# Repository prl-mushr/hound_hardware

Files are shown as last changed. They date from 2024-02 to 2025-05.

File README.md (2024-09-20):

# Repository that contains hardware files associated to the HOUND project.
##### Note: If you already have a [MuSHR](https://mushr.io/), you will be re-using a fair number of the components, so do not order the highlighted components from the BOM, as they represent the "overlapping components". Additionally, you may want to order the d455 if you don't have one and want to use that.

## [Bill of materials](https://docs.google.com/spreadsheets/d/12jod9aALWGB2n3a47guYzTRTLul8M2QtT9iCGtkBhws/edit?usp=sharing)

## Build steps:
The build steps are divided into 2 parts:
1. Setting up the computers -- flashing Jetpack and the ardupilot board
2. Setting up the HOUND hardware

### Setting up the Jetson Orin NX:

1. For this, you will require one Desktop, and the Orin NX, along with its corresponding parts (WiFi card, SSD, heat sink). After that, follow [this video](https://www.youtube.com/watch?v=Ucg5Zqm9ZMk) to flash the operating system onto the module, but flash jetpack 5.1.2.
2. Due to bugs in the SDK manager, the SDK manager will likely flash the operating system, but fail to properly install the jetpack. If this happens, you just need to do the following:
   ```bash
    sudo apt update
    sudo apt-get install nvidia-jetpack
    sudo usermod -aG docker $USER
    sudo pip install jetson-stats
    sudo reboot now
    ```
3. For Ubuntu, download QGroundcontrol(QGC), for Windows (preferred), download MissionPlanner(MP).
4. Follow these instructions for [QGC](https://docs.qgroundcontrol.com/Stable_V4.3/en/qgc-user-guide/setup_view/firmware.html) and these for [MP](https://ardupilot.org/planner/docs/common-loading-firmware-onto-pixhawk.html) to flash the [custom firmware](https://github.com/prl-mushr/hound_hardware/tree/main/ardupilot_files/firmwares/mroPixracerPro) on to the MRo PixRacer Pro.
5. Follow this guide to load the [board parameters](https://github.com/prl-mushr/hound_hardware/blob/main/ardupilot_files/parameters/HOUND_mro_defaults.param) using QGC or MP onto the MRo Pixracer pro. (**TODO: insert images describing this step**)

### Setting up the Hardware:
#### Setting up the base (These steps are a WIP and will be updated as we have people in our lab build more of these platforms while trying to follow these instructions). 
We re-use some of the build steps for the MuSHR to set up the low-level platform. Follow the instructions [here](https://mushr.io/hardware/build_instructions/#servo-motor-removal) for the following components:
1. [VESC Preparation](https://mushr.io/hardware/build_instructions/#vesc-preparation): Follow the steps up to step "20", where the VESC firmware is uploaded. 
    - Instead of uploading the servo output bin file, use the [default firmware](https://github.com/prl-mushr/hound_hardware/blob/main/VESC_files/firmwares/hw_410_411_412/VESC_default.bin).
    - Instead of soldering the banana connectors, you will be soldering the IC3 connectors instead, and you will be soldering the leads from the two Matek buck converters into the same IC3 connectors, such that the VESC and the Matek buck converters are all able to get power from the same IC3 connectors. Use the color of the wire to infer polarity, red for positive, black for negative.
    Pictures for reference (make sure to strip the wire down to 14-16 gauge):
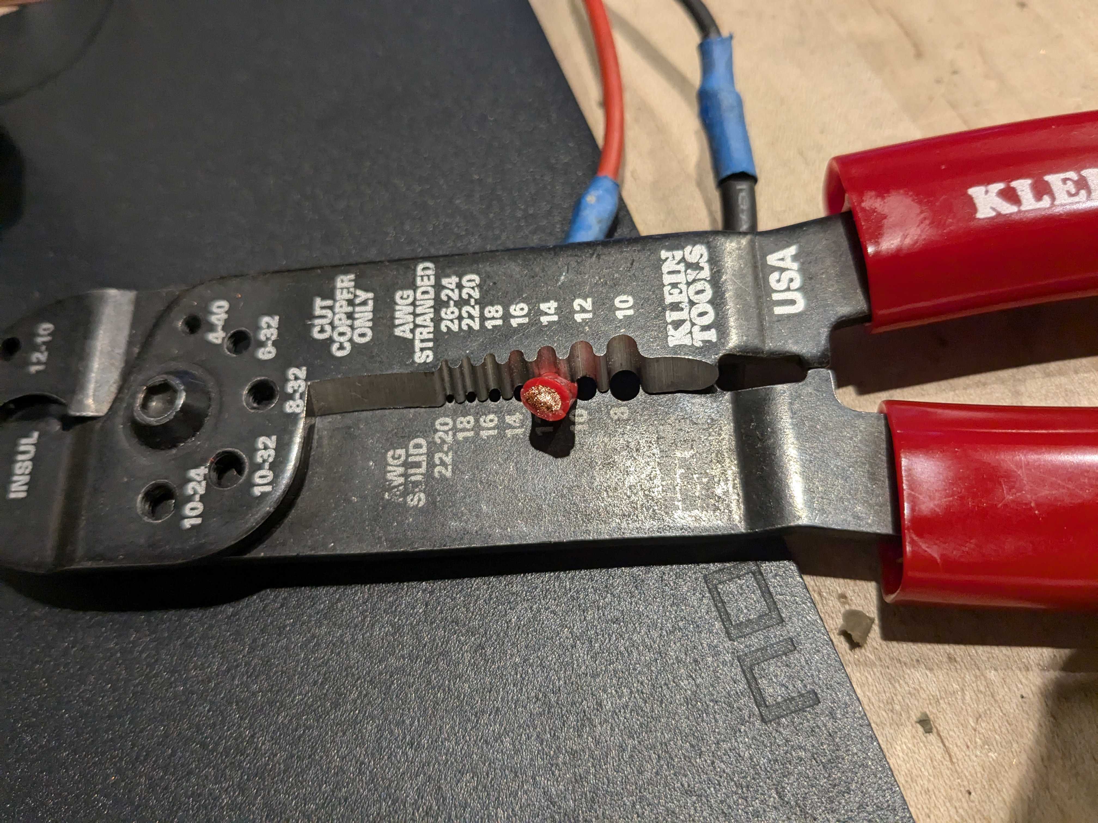
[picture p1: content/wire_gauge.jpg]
    
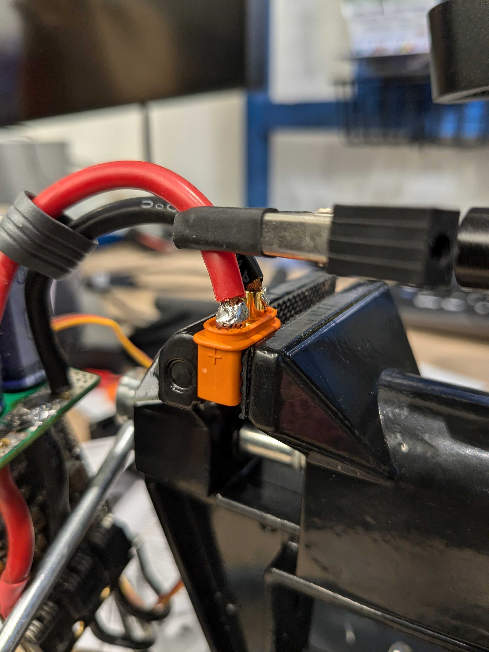
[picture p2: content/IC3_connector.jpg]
    
    - Using the [BLDC tool](https://github.com/vedderb/bldc-tool/tree/master) (git clone, build), upload the [hound_vesc.xml](https://github.com/prl-mushr/hound_hardware/blob/main/VESC_files/parameters/hound_vesc.xml) parameter file.
    - You may have to set up the PPM input. For this, in the bldc-tool, go to the app configuration --> PPM and set the values as shown in the image.
    - 

2. [Servo removal](https://mushr.io/hardware/build_instructions/#servo-motor-removal) and [Servo installation](https://mushr.io/hardware/build_instructions/#servo-motor-installation): Instead of throwing away the servo mount that comes with the car, attach the new, high torque sevo to it, and attach the mount back into the car. We will center the servo later, but it if you know how to center the servo, you can do it at this step as well. (**TODO: insert images describing this step**)
3. [Brushed motor removal](https://mushr.io/hardware/build_instructions/#brushed-motor-removal): Follow the steps exactly.
4. [Brushless motor installation](https://mushr.io/hardware/build_instructions/#brushless-motor-installation): Follow the instructions, however, after closing the gearbox casing, apply a bead of hot-glue along the line separating the two parts of the case, outlined in green on all sides (left, top, right). Ignore the red circles around the screws. This is done to prevent small rocks from getting into the gearbox and jamming it. (**TODO: insert images describing this step**)

<p align="center">
  
</p>

5. Setting up the Remote controller. Follow the instructions [here](https://www.youtube.com/watch?v=lxE4K7ghST0) for setting up the transmitter and receiver. Particularly, follow the instructions for:
  - [Binding](https://www.youtube.com/watch?v=lxE4K7ghST0&t=64s)
  - [Setting up the failsafe](https://www.youtube.com/watch?v=lxE4K7ghST0&t=101s) (very important!)
  - [Setting up Aux channels](https://www.youtube.com/watch?v=lxE4K7ghST0&t=203s): Set channel 5 to Switch C, channel 6 to Switch D
  - [Changing the output from PWM to PPM](https://www.youtube.com/watch?v=lxE4K7ghST0&t=468s)

#### Setting up the Lower Base:
1. Attach the front base and the rear base to the vehicle platform using the M3x40 screws
<p align="center">
  
</p>

2. Attach the front cover to the front base using the M4x40 screws
<p align="center">
  
</p>
3. Mount the VESC, exhaust fan on the rear base, and place the buck converters and R/C receiver using double sided tape as shown. Pass the motor cables through the whole marked on the right. Use the same hole to pass in the servo wires from underneath. Connect the VESC's USB wire, which will be attached to the Jetson later.

#### Note: the VESC is mounted using 10 mm standoffs. The USB port of the VESC should be facing towards the buck converters. When mounted in this pose, the capacitor bank should automatically swing away from the standoffs of the VESC. If you mount it such that the VESC is on 20 mm standoffs and the USB port is facing the jetson, the capacitor bank terminals can short against the standoffs. This alternate orientation requires use of plastic standoffs or additional insulation around the capacitor bank (hot glue works).
<p align="center">

</p>

4. Wiring:
    - Connect the other buck converter's output to the R/C receiver.
    - Using the mro pixracer pro [pinout](https://docs.mrobotics.io/autopilots/pixracer-pro.html#pinout) for reference:
      - Connect one of the Matek buck converter's 5V output to the Power rail on the MRo Pixracer pro's power rail.
      - The Power rail has Ground at the bottom, 5 V in the middle, and the signal on top.
      - Connect the steering servo wire to channel 4, and VESC wire to channel 3. Remove/cut the VESC wire's 5V line before connecting. You will likely need to use an extension wire for the servo (also included in the BOM)
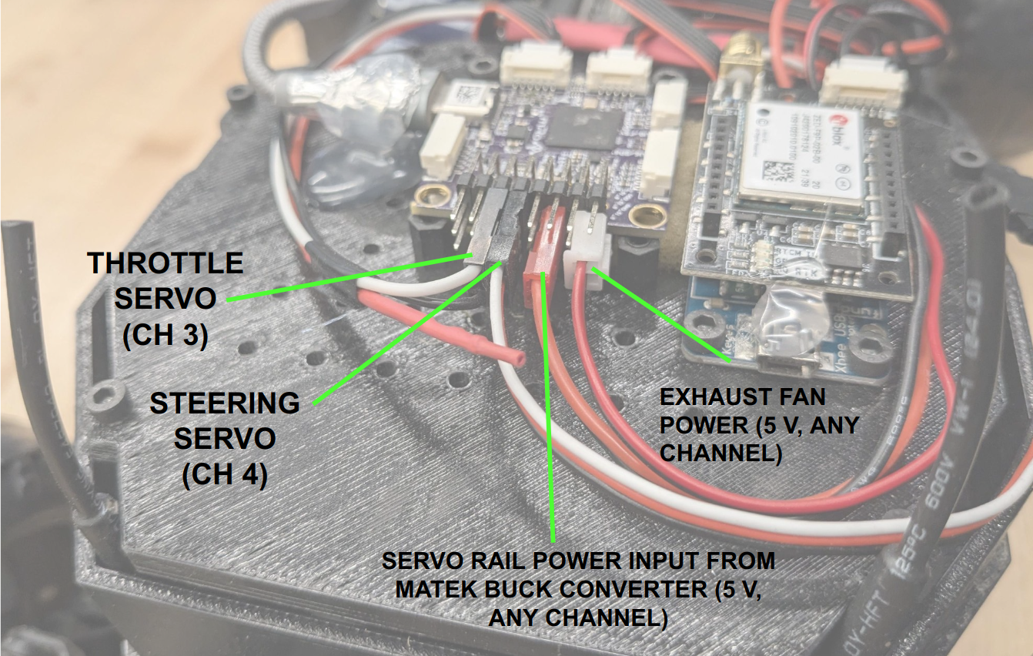
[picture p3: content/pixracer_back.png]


5. Mount the Mid-level on the rear base using the M3x30 standoffs
<p align="center">

</p>

6. Mount the Mro Pixracer Pro as shown
Images for reference:
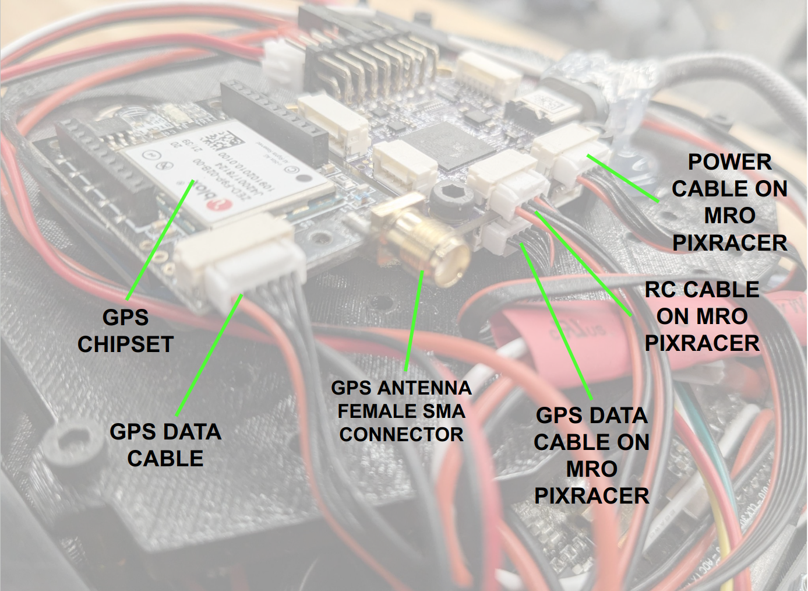
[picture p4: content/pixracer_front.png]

<p align="center">

</p>

7. Mount the D455 to the front cover as shown using the M4x8 screws
<p align="center">

</p>

8. Mount the lidar_mount_left and lidar_mount_right to the YDLiDAR as shown using M3x10 screws.
<p align="center">

</p>

9. Mount the LiDAR to the mid-section using M3x10 screws.
<p align="center">

</p>

10. Attach the mid-section to the front cover as shown
<p align="center">
  
</p>

12. Attach the rear cover to the rear base as shown.
<p align="center">

</p>

13. Mount the GPS to the GPS cover and put Aluminum tape under it: 
Image for reference:
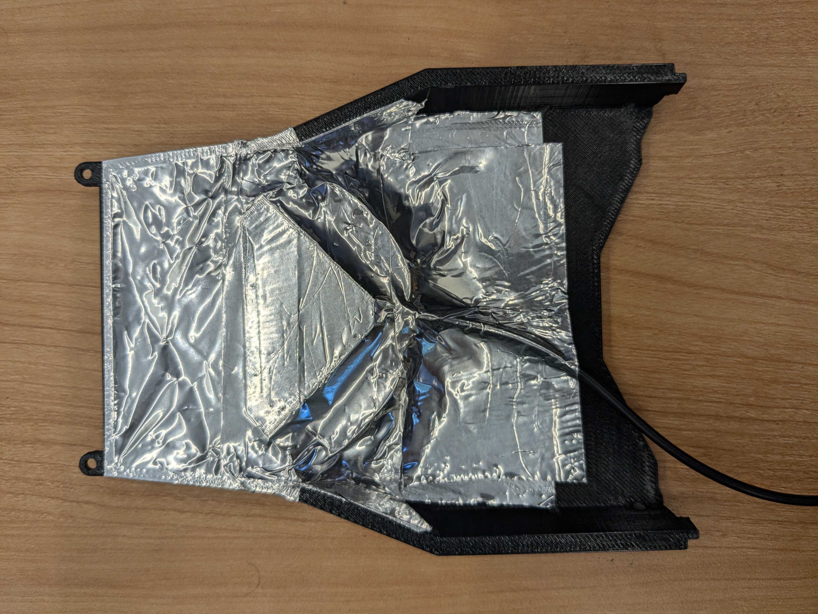
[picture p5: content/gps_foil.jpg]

<p align="center">

</p>

14. We use the latches and pins to attach the rear cover and the GPS cover as shown. There are latch holders on the mid-section as well. (**TODO: this step needs more sub-steps with images as it is not obvious how to attach the spring in the latch to the pin.**)
<p align="center">

</p>

15. In the holes shown here, first screw in the M2.5x5 standoffs. Then, mount the Jetson Orin NX to the standoffs using M2.5x5 screws.
<p align="center">

</p>

16. Connect the USB cables for all the devices as shown in the following images:
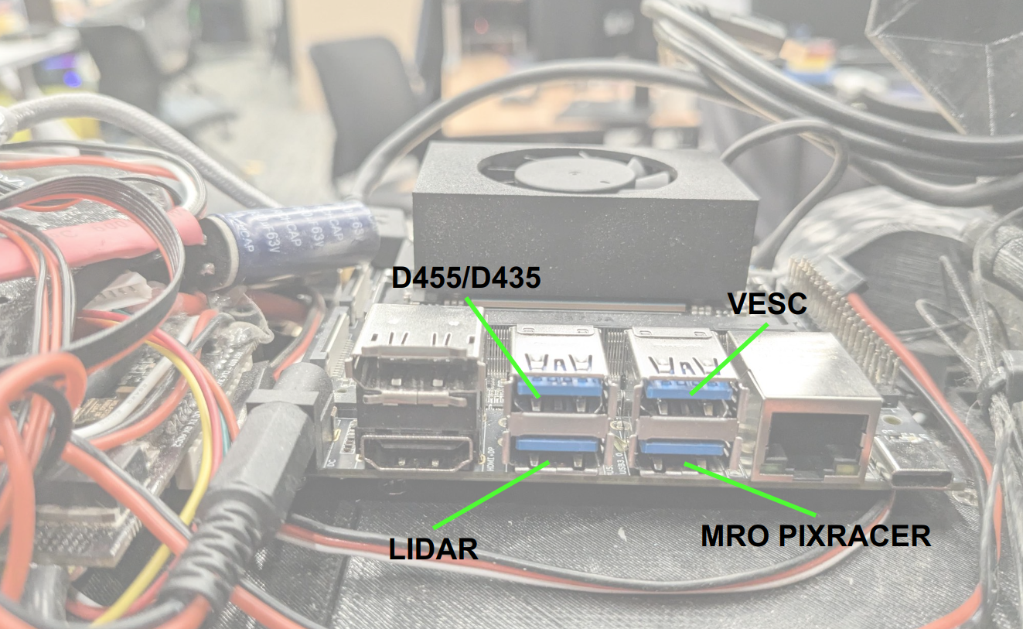
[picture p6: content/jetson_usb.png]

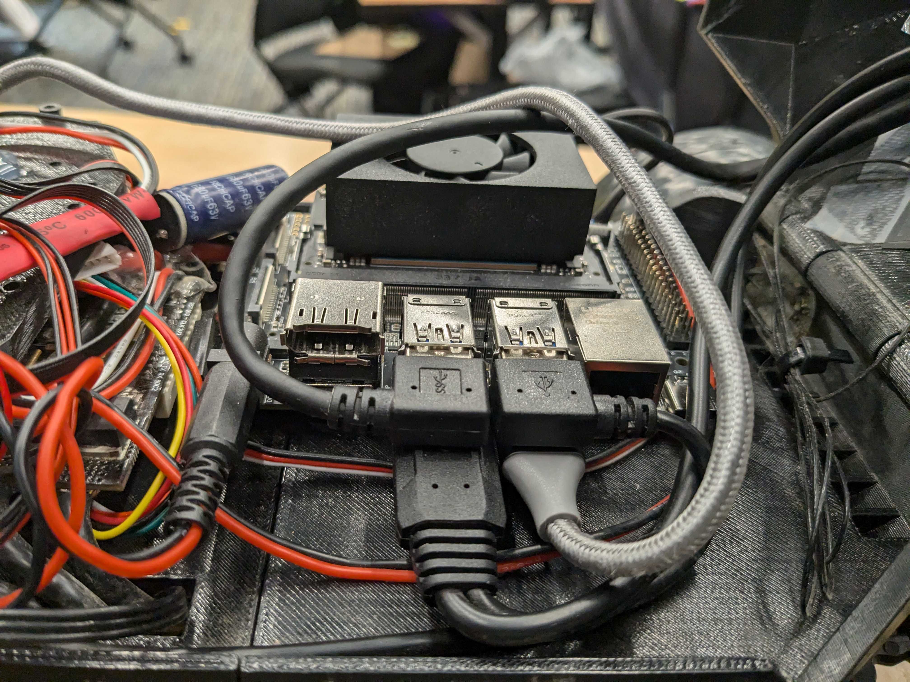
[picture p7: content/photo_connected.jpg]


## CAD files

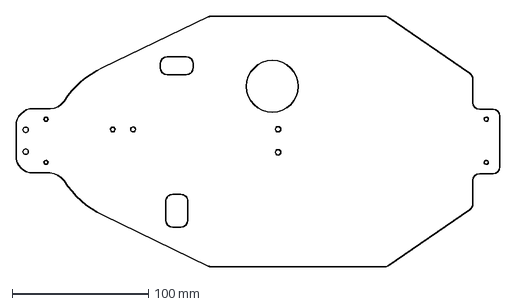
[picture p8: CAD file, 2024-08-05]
3D_files/traxass_adapter.dxf
355.3 x 184.0 mm

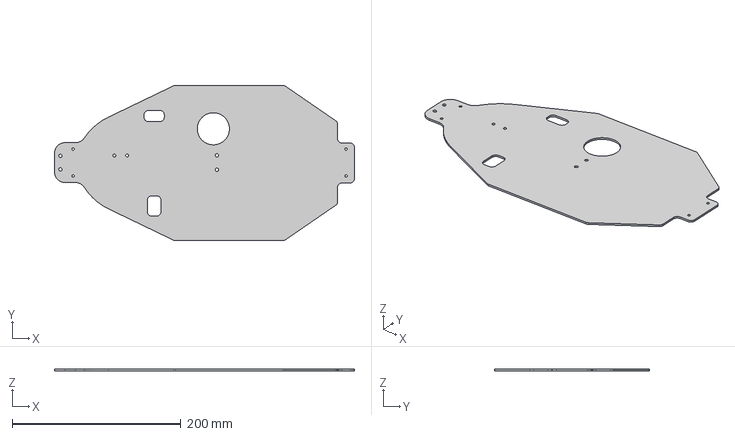
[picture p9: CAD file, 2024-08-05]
3D_files_MuSHR_V4/traxass_adapter v2.step
355.3 x 184.0 x 2.00 mm

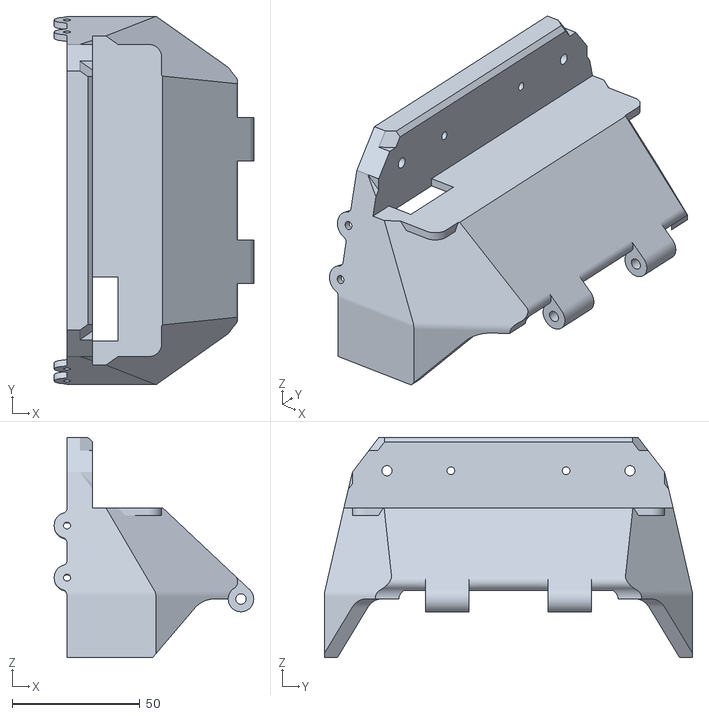
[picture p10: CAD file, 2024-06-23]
3D_files/Front_cover V4.stl
78.0 x 144.0 x 86.0

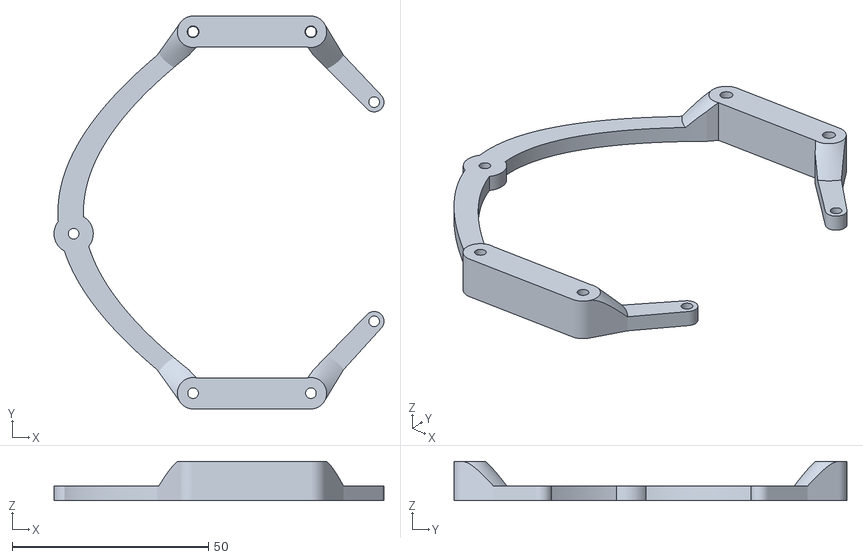
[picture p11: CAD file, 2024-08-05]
3D_files_MuSHR_V4/LIDAR mount new.stl
84.0 x 100.0 x 10.0

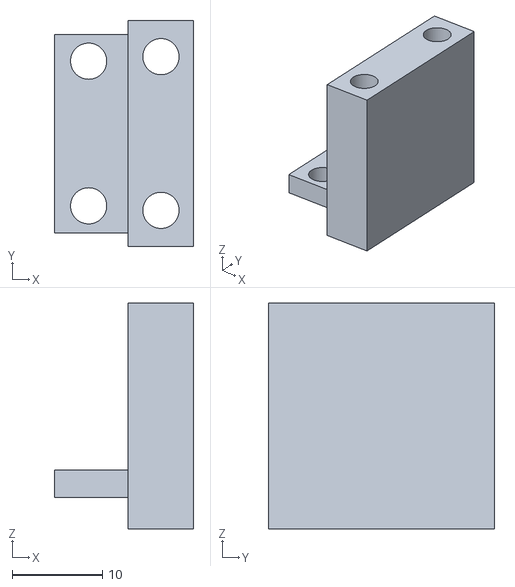
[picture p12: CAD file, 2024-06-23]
3D_files/rear chassis mount.stl
15.4 x 25.0 x 25.0

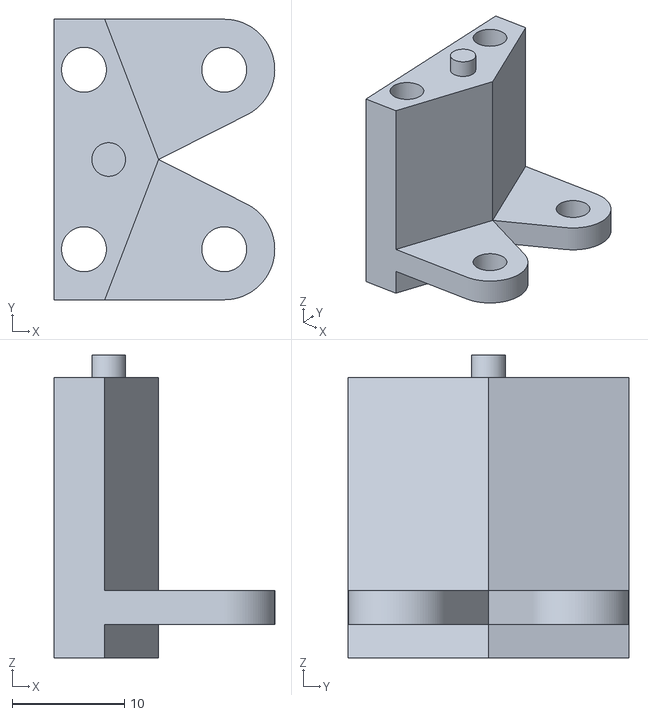
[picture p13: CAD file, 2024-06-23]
3D_files_MuSHR_V4/front_chassis_mount.stl
19.6 x 25.0 x 27.0

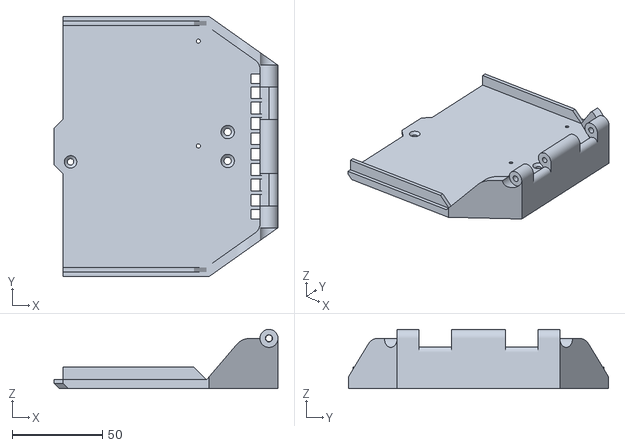
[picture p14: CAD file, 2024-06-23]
3D_files_MuSHR_V4/Front_base.stl
124.0 x 144.0 x 32.9

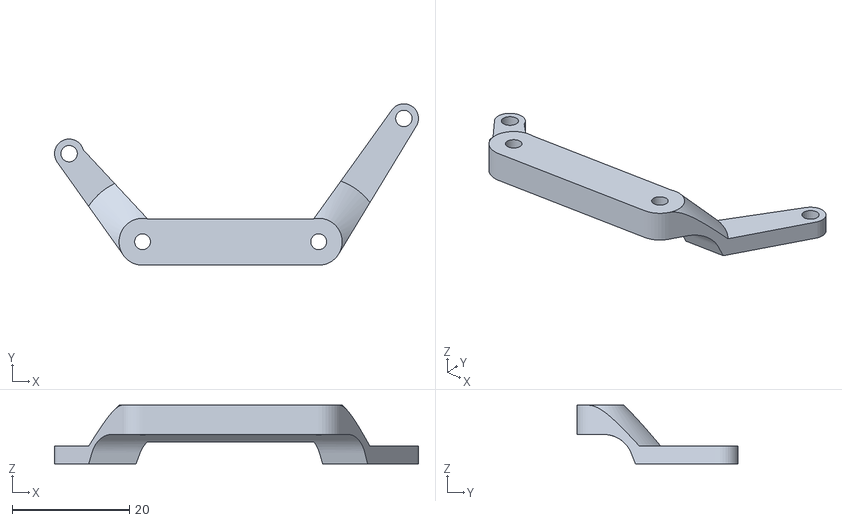
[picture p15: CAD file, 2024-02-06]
3D_files/LiDAR mount right.stl
62.0 x 27.5 x 10.0

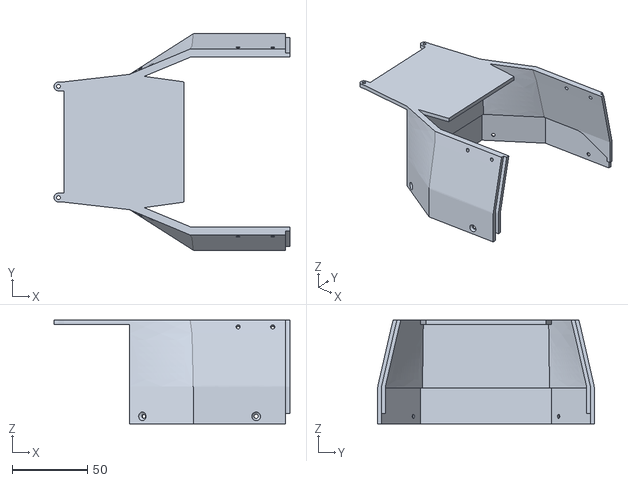
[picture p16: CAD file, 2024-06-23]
3D_files_MuSHR_V4/Rear_cover.stl
157.0 x 144.0 x 69.0

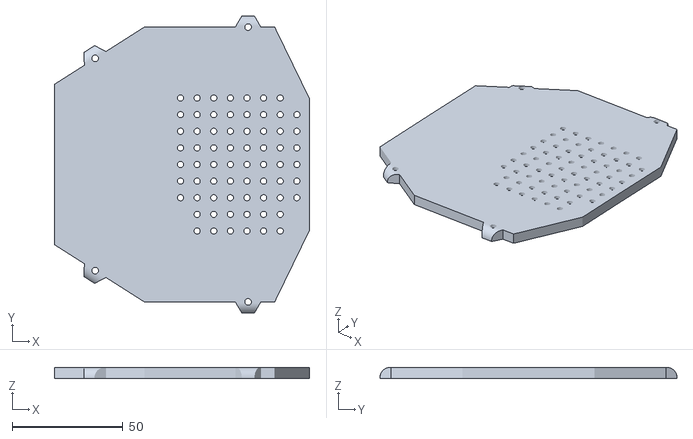
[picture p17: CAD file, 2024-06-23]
3D_files_MuSHR_V4/Mid_level.stl
115.1 x 134.0 x 5.00

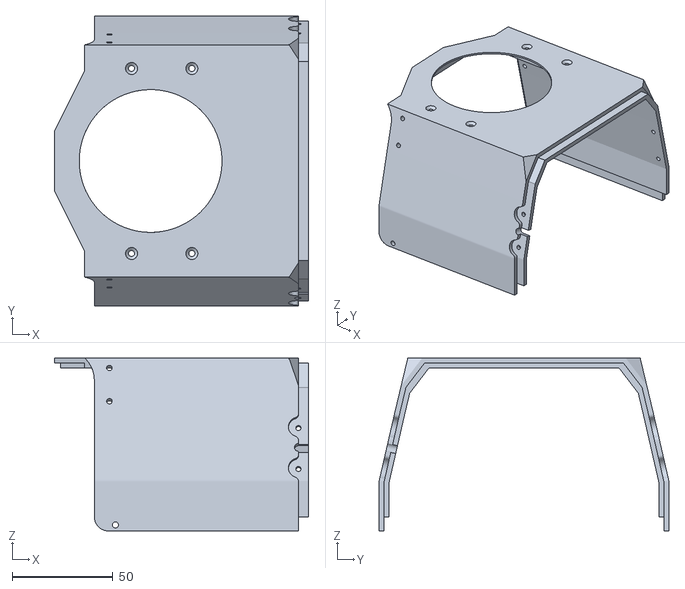
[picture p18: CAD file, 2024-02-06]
3D_files/Mid_cover_spotter.stl
126.3 x 144.0 x 86.0

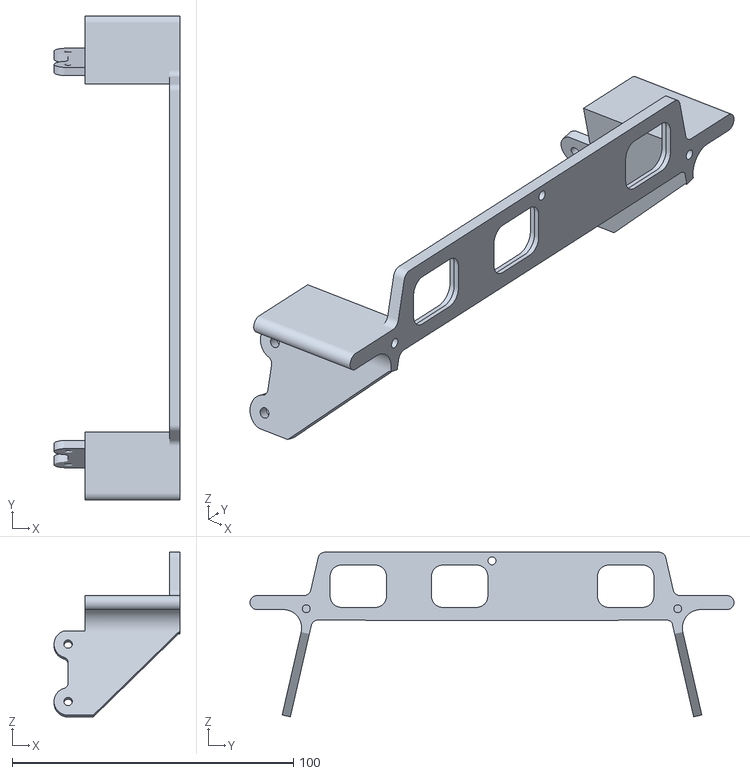
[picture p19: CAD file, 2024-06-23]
3D_files_MuSHR_V4/spotter_holder.stl
44.8 x 172.0 x 58.5

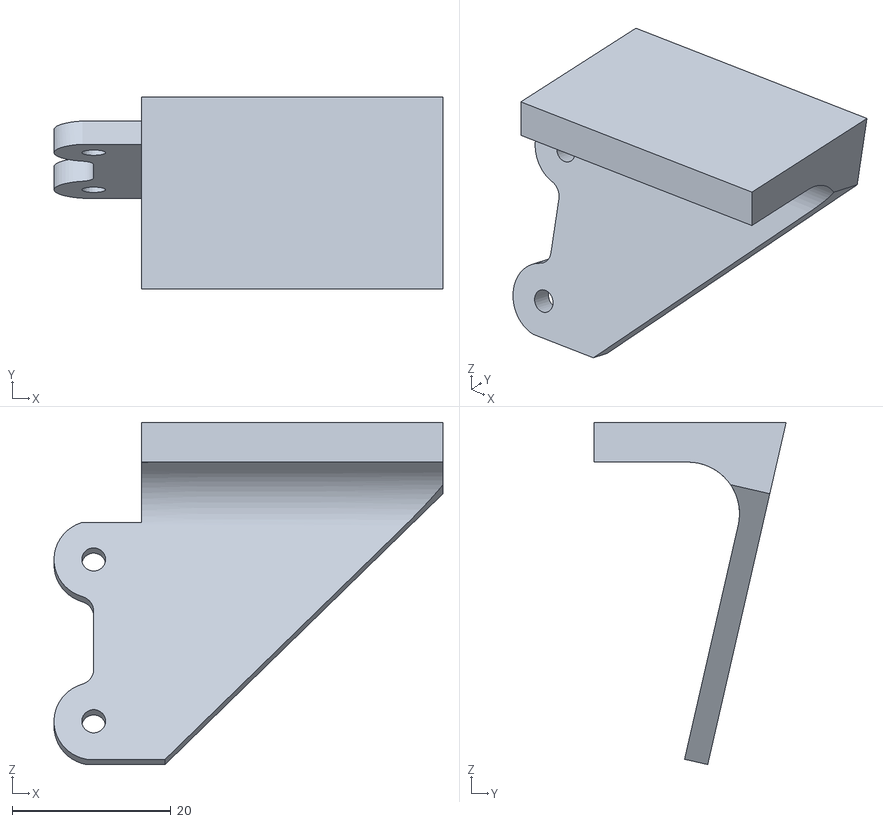
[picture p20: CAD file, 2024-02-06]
3D_files/spotter_holder.stl
49.0 x 24.2 x 43.1

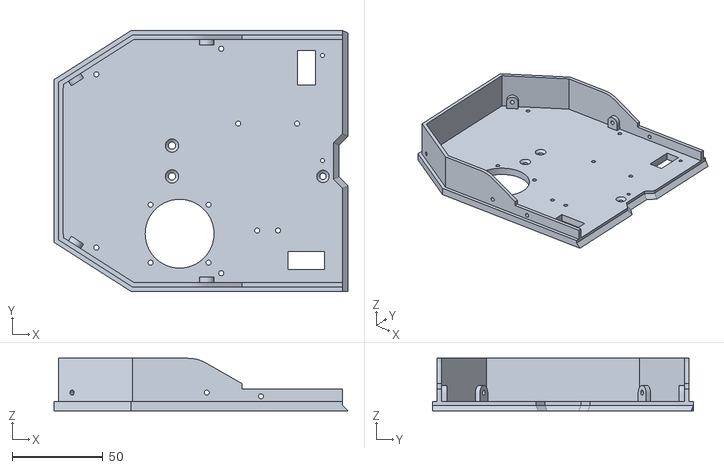
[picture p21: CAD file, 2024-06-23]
3D_files_MuSHR_V4/Rear_base.stl
162.4 x 144.0 x 29.0

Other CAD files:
3D_files/Front_cover d455.stl
3D_files_MuSHR_V4/LiDAR mount right.stl
3D_files/Rear_cover.stl
3D_files/Front_base.stl
3D_files/GPS_cover.stl
3D_files/LiDAR mount left.stl
3D_files/Mid_cover.stl
3D_files/Rear_base.stl
3D_files_MuSHR_V4/GPS_cover.stl
3D_files_MuSHR_V4/LiDAR mount left.stl
3D_files_MuSHR_V4/Mid_cover_spotter.stl
3D_files_MuSHR_V4/lidar_ftdi_holder_mirror.stl
3D_files_MuSHR_V4/lock pin.stl
3D_files_MuSHR_V4/lock_mid.stl
3D_files_MuSHR_V4/lock_rear.stl

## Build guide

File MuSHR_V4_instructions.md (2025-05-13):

# MuSHR V4 build instructions (Draft).
##### Note: If you already have a [MuSHR](https://mushr.io/), you will be re-using a fair number of the components, so do not order the highlighted components from the BOM, as they represent the "overlapping components". Additionally, you may want to order the d455 if you don't have one and want to use that.

## [Bill of materials](https://docs.google.com/spreadsheets/d/12jod9aALWGB2n3a47guYzTRTLul8M2QtT9iCGtkBhws/edit?usp=sharing)

## Build steps:
The build steps are divided into 2 parts:
1. Setting up the computers -- flashing Jetpack and the ardupilot board
2. Setting up the HOUND hardware

### Setting up the Jetson Orin NX:

1. For this, you will require one Desktop, and the Orin NX, along with its corresponding parts (WiFi card, SSD, heat sink). After that, follow [this video](https://www.youtube.com/watch?v=Ucg5Zqm9ZMk) to flash the operating system onto the module, but flash jetpack 5.1.2.
2. Due to bugs in the SDK manager, the SDK manager will likely flash the operating system, but fail to properly install the jetpack. If this happens, you just need to do the following:
   ```bash
    sudo apt update
    sudo apt-get install nvidia-jetpack
    sudo usermod -aG docker $USER
    sudo pip install jetson-stats
    sudo reboot now
    ```

### Setting up the Hardware:
#### Setting up the base (These steps are a WIP and will be updated as we have people in our lab build more of these platforms while trying to follow these instructions). 
We re-use some of the build steps for the MuSHR to set up the low-level platform. Follow the instructions [here](https://mushr.io/hardware/build_instructions/#servo-motor-removal) for the following components:
1. [VESC Preparation](https://mushr.io/hardware/build_instructions/#vesc-preparation): Follow these steps to upload the VESC firmware. 
    - Instead of soldering the banana connectors, you will be soldering the IC3 connectors instead. Use the color of the wire to infer polarity, red for positive, black for negative.
    Pictures for reference (make sure to strip the wire down to 14-16 gauge):
    
    
    - Using the [BLDC tool](https://github.com/vedderb/bldc-tool/tree/master) (git clone, build), upload the [mushr_vesc_sensorless_config.xml](https://github.com/prl-mushr/vesc/blob/master/vesc_configs/mushr_vesc_sensorless_config.xml) parameter file.

2. [Servo removal](https://mushr.io/hardware/build_instructions/#servo-motor-removal) and [Servo installation](https://mushr.io/hardware/build_instructions/#servo-motor-installation): Instead of throwing away the servo mount that comes with the car, attach the new servo to the existing mount and attach the mount back into the car. (**TODO: reminder to center the servo!**)
3. [Brushed motor removal](https://mushr.io/hardware/build_instructions/#brushed-motor-removal): Follow the steps exactly.
4. [Brushless motor installation](https://mushr.io/hardware/build_instructions/#brushless-motor-installation): Follow the steps exactly

<p align="center">
  
</p>

5. Setting up the Remote controller with the Jetson: Follow the instructions in step 13 of the [Software setup](https://mushr.io/hardware/build_instructions/#software-setup).
Depending on your controller and exact servo spec, you may also need to follow steps 14 and 15.

7. Additionally, you may set up the Wi-Fi set up as indicated in steps 1-4 of the software setup.

#### Setting up the Lower Base:
1. First, the [front](https://github.com/prl-mushr/hound_hardware/blob/main/3D_files_MuSHR_V4/front_chassis_mount.stl) and [rear](https://github.com/prl-mushr/hound_hardware/blob/main/3D_files_MuSHR_V4/rear%20chassis%20mount.stl)
are mounted to the car using M3x10 screws. Then attach the front base and the rear base to the vehicle platform using the M3x40 screws as shown in the image.
(**TODO: this might need an image**)

<p align="center">
  
</p>

2. Attach the front cover to the front base using the M4x40 screws
<p align="center">
  
</p>

3. Follow the following reference diagram for wiring
connection_diagram

4. Mount the VESC, exhaust fan on the rear base, and place the buck converters and R/C receiver using double sided tape as shown. Pass the motor cables through the whole marked on the right. Use the same hole to pass in the servo wires from underneath. Connect the VESC's USB wire, which will be attached to the Jetson later.
**TODO: insert image for how to mount VESC with the standoffs**.

<p align="center">

</p>

5. Mount the D455 to the front cover as shown using the M4x8 screws
<p align="center">

</p>

6. Mount the lidar_mount_left and lidar_mount_right to the YDLiDAR as shown using M3x10 screws. **TODO: this needs images**
<p align="center">

</p>

7. Mount the LiDAR to the mid-section using M3x10 screws.
<p align="center">

</p>

8. Attach the mid-section to the front cover as shown
<p align="center">
  
</p>

9. Attach the rear cover to the rear base as shown.
<p align="center">

</p>

11. We use the latches and pins to attach the rear cover and the rear cover as shown. There are latch holders on the mid-section as well. (**TODO: this step needs more sub-steps with images as it is not obvious how to attach the spring in the latch to the pin.**)
<p align="center">

</p>

12. In the holes shown here, first screw in the M2.5x5 standoffs. Then, mount the Jetson Orin NX to the standoffs using M2.5x5 screws.
<p align="center">

</p>

16. Connect the USB cables for all the devices.

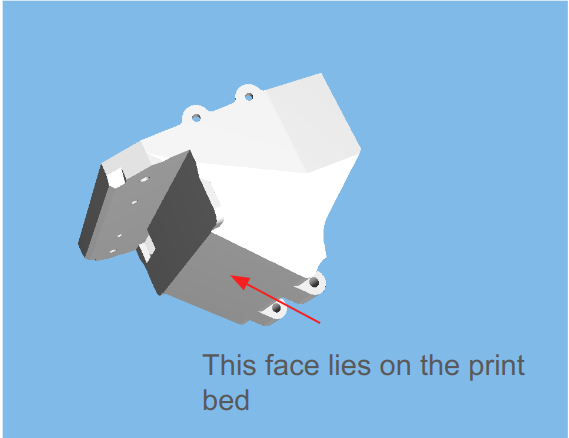
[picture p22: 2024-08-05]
3D_files_MuSHR_V4/Front_cover_print_orientation.png

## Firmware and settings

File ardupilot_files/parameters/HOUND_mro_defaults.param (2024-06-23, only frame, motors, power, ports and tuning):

ATC_SPEED_D,0
ATC_SPEED_FF,0
ATC_SPEED_FLTD,0
ATC_SPEED_FLTE,10
ATC_SPEED_FLTT,0
ATC_SPEED_I,0.2
ATC_SPEED_IMAX,1
ATC_SPEED_P,0.2
ATC_SPEED_SMAX,0
ATC_STR_ACC_MAX,120
ATC_STR_ANG_P,2
ATC_STR_RAT_D,0
ATC_STR_RAT_FF,0.2
ATC_STR_RAT_FLTD,0
ATC_STR_RAT_FLTE,10
ATC_STR_RAT_FLTT,0
ATC_STR_RAT_I,0
ATC_STR_RAT_IMAX,1
ATC_STR_RAT_MAX,120
ATC_STR_RAT_P,0.2
ATC_STR_RAT_SMAX,0
BATT_AMP_OFFSET,0
BATT_AMP_PERVLT,17
BATT_ARM_MAH,0
BATT_ARM_VOLT,0
BATT_CAPACITY,3300
BATT_CRT_MAH,0
BATT_CRT_VOLT,0
BATT_CURR_PIN,15
BATT_FS_CRT_ACT,0
BATT_FS_LOW_ACT,0
BATT_FS_VOLTSRC,0
BATT_LOW_MAH,0
BATT_LOW_TIMER,10
BATT_LOW_VOLT,0
BATT_MONITOR,4
BATT_OPTIONS,0
BATT_SERIAL_NUM,-1
BATT_VLT_OFFSET,0
BATT_VOLT_MULT,10.1
BATT_VOLT_PIN,14
BATT2_MONITOR,0
BATT3_MONITOR,0
BATT4_MONITOR,0
BATT5_MONITOR,0
BATT6_MONITOR,0
BATT7_MONITOR,0
BATT8_MONITOR,0
BATT9_MONITOR,0
FRAME_CLASS,1
FRAME_TYPE,0
INS_GYRO_FILTER,20
INS_HNTCH_ENABLE,0
MOT_PWM_FREQ,16
MOT_PWM_TYPE,0
MOT_SAFE_DISARM,0
MOT_SLEWRATE,0
MOT_SPD_SCA_BASE,1
MOT_STR_THR_MIX,0.5
MOT_THR_MAX,100
MOT_THR_MIN,0
MOT_THST_EXPO,0
MOT_VEC_ANGLEMAX,0
SERIAL0_BAUD,1500
SERIAL0_PROTOCOL,2
SERIAL1_BAUD,921
SERIAL1_OPTIONS,0
SERIAL1_PROTOCOL,2
SERIAL2_BAUD,57
SERIAL2_OPTIONS,0
SERIAL2_PROTOCOL,2
SERIAL3_BAUD,230
SERIAL3_OPTIONS,0
SERIAL3_PROTOCOL,5
SERIAL4_BAUD,38
SERIAL4_OPTIONS,0
SERIAL4_PROTOCOL,5
SERIAL5_BAUD,57
SERIAL5_OPTIONS,0
SERIAL5_PROTOCOL,-1
SERIAL6_BAUD,57
SERIAL6_OPTIONS,0
SERIAL6_PROTOCOL,22
SERIAL7_BAUD,115200
SERIAL7_OPTIONS,0
SERIAL7_PROTOCOL,2
SERVO1_FUNCTION,0
SERVO1_MAX,1900
SERVO1_MIN,1100
SERVO1_REVERSED,0
SERVO1_TRIM,1500
SERVO2_FUNCTION,0
SERVO2_MAX,1900
SERVO2_MIN,1100
SERVO2_REVERSED,0
SERVO2_TRIM,1500
SERVO3_FUNCTION,70
SERVO3_MAX,2000
SERVO3_MIN,1000
SERVO3_REVERSED,0
SERVO3_TRIM,1050
SERVO4_FUNCTION,26
SERVO4_MAX,1770
SERVO4_MIN,1230
SERVO4_REVERSED,0
SERVO4_TRIM,1500
SERVO5_FUNCTION,0
SERVO5_MAX,1900
SERVO5_MIN,1100
SERVO5_REVERSED,0
SERVO5_TRIM,1500
SERVO6_FUNCTION,0
SERVO6_MAX,1900
SERVO6_MIN,1100
SERVO6_REVERSED,0
SERVO6_TRIM,1500
SERVO7_FUNCTION,0
SERVO7_MAX,1900
SERVO7_MIN,1100
SERVO7_REVERSED,0
SERVO7_TRIM,1500
SERVO8_FUNCTION,0
SERVO8_MAX,1900
SERVO8_MIN,1100
SERVO8_REVERSED,0
SERVO8_TRIM,1500
SERVO9_FUNCTION,0
SERVO9_MAX,1900
SERVO9_MIN,1100
SERVO9_REVERSED,0
SERVO9_TRIM,1500

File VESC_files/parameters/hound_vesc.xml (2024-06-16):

<?xml version="1.0" encoding="UTF-8"?>
<MCConfiguration>
    <pwm_mode>1</pwm_mode>
    <comm_mode>0</comm_mode>
    <motor_type>0</motor_type>
    <sensor_mode>0</sensor_mode>
    <l_current_max>75</l_current_max>
    <l_current_min>-75</l_current_min>
    <l_in_current_max>100</l_in_current_max>
    <l_in_current_min>-100</l_in_current_min>
    <l_abs_current_max>150</l_abs_current_max>
    <l_min_erpm>-2000</l_min_erpm>
    <l_max_erpm>100000</l_max_erpm>
    <l_max_erpm_fbrake>100000</l_max_erpm_fbrake>
    <l_max_erpm_fbrake_cc>100000</l_max_erpm_fbrake_cc>
    <l_min_vin>13</l_min_vin>
    <l_max_vin>57</l_max_vin>
    <l_battery_cut_start>10</l_battery_cut_start>
    <l_battery_cut_end>8</l_battery_cut_end>
    <l_slow_abs_current>1</l_slow_abs_current>
    <l_rpm_lim_neg_torque>1</l_rpm_lim_neg_torque>
    <l_temp_fet_start>80</l_temp_fet_start>
    <l_temp_fet_end>100</l_temp_fet_end>
    <l_temp_motor_start>80</l_temp_motor_start>
    <l_temp_motor_end>100</l_temp_motor_end>
    <l_min_duty>0.005</l_min_duty>
    <l_max_duty>0.95</l_max_duty>
    <sl_min_erpm>150</sl_min_erpm>
    <sl_min_erpm_cycle_int_limit>1100</sl_min_erpm_cycle_int_limit>
    <sl_max_fullbreak_current_dir_change>10</sl_max_fullbreak_current_dir_change>
    <sl_cycle_int_limit>62</sl_cycle_int_limit>
    <sl_cycle_int_limit_high_fac>0.8</sl_cycle_int_limit_high_fac>
    <sl_cycle_int_rpm_br>80000</sl_cycle_int_rpm_br>
    <sl_bemf_coupling_k>600</sl_bemf_coupling_k>
    <hall_table_0>-1</hall_table_0>
    <hall_table_1>1</hall_table_1>
    <hall_table_2>3</hall_table_2>
    <hall_table_3>2</hall_table_3>
    <hall_table_4>5</hall_table_4>
    <hall_table_5>6</hall_table_5>
    <hall_table_6>4</hall_table_6>
    <hall_table_7>-1</hall_table_7>
    <hall_sl_erpm>1000</hall_sl_erpm>
    <foc_current_kp>0.03</foc_current_kp>
    <foc_current_ki>50</foc_current_ki>
    <foc_f_sw>20000</foc_f_sw>
    <foc_dt_us>0.08</foc_dt_us>
    <foc_encoder_inverted>0</foc_encoder_inverted>
    <foc_encoder_offset>180</foc_encoder_offset>
    <foc_encoder_ratio>7</foc_encoder_ratio>
    <foc_sensor_mode>0</foc_sensor_mode>
    <foc_pll_kp>2000</foc_pll_kp>
    <foc_pll_ki>20000</foc_pll_ki>
    <foc_motor_l>7e-06</foc_motor_l>
    <foc_motor_r>0.015</foc_motor_r>
    <foc_motor_flux_linkage>0.00245</foc_motor_flux_linkage>
    <foc_observer_gain>9e+07</foc_observer_gain>
    <foc_duty_dowmramp_kp>10</foc_duty_dowmramp_kp>
    <foc_duty_dowmramp_ki>200</foc_duty_dowmramp_ki>
    <foc_openloop_rpm>1200</foc_openloop_rpm>
    <foc_sl_openloop_hyst>0.5</foc_sl_openloop_hyst>
    <foc_sl_openloop_time>0.5</foc_sl_openloop_time>
    <foc_sl_d_current_duty>0</foc_sl_d_current_duty>
    <foc_sl_d_current_factor>0</foc_sl_d_current_factor>
    <foc_hall_table_0>255</foc_hall_table_0>
    <foc_hall_table_1>255</foc_hall_table_1>
    <foc_hall_table_2>255</foc_hall_table_2>
    <foc_hall_table_3>255</foc_hall_table_3>
    <foc_hall_table_4>255</foc_hall_table_4>
    <foc_hall_table_5>255</foc_hall_table_5>
    <foc_hall_table_6>255</foc_hall_table_6>
    <foc_hall_table_7>255</foc_hall_table_7>
    <foc_sl_erpm>2500</foc_sl_erpm>
    <s_pid_kp>0.0001</s_pid_kp>
    <s_pid_ki>0.015</s_pid_ki>
    <s_pid_kd>0</s_pid_kd>
    <s_pid_min_rpm>900</s_pid_min_rpm>
    <p_pid_kp>0.03</p_pid_kp>
    <p_pid_ki>0</p_pid_ki>
    <p_pid_kd>0.0004</p_pid_kd>
    <p_pid_ang_div>1</p_pid_ang_div>
    <cc_startup_boost_duty>0.1</cc_startup_boost_duty>
    <cc_min_current>1</cc_min_current>
    <cc_gain>0.001</cc_gain>
    <cc_ramp_step_max>50</cc_ramp_step_max>
    <m_fault_stop_time_ms>1000</m_fault_stop_time_ms>
    <m_duty_ramp_step>0.02</m_duty_ramp_step>
    <m_duty_ramp_step_rpm_lim>0.0005</m_duty_ramp_step_rpm_lim>
    <m_current_backoff_gain>0.5</m_current_backoff_gain>
    <m_encoder_counts>8192</m_encoder_counts>
    <m_sensor_port_mode>0</m_sensor_port_mode>
    <meta_description>&lt;!DOCTYPE HTML PUBLIC &quot;-//W3C//DTD HTML 4.0//EN&quot; &quot;http://www.w3.org/TR/REC-html40/strict.dtd&quot;&gt;
&lt;html&gt;&lt;head&gt;&lt;meta name=&quot;qrichtext&quot; content=&quot;1&quot; /&gt;&lt;style type=&quot;text/css&quot;&gt;
p, li { white-space: pre-wrap; }
&lt;/style&gt;&lt;/head&gt;&lt;body style=&quot; font-family:'Ubuntu'; font-size:11pt; font-weight:400; font-style:normal;&quot;&gt;
&lt;p style=&quot; margin-top:0px; margin-bottom:0px; margin-left:0px; margin-right:0px; -qt-block-indent:0; text-indent:0px;&quot;&gt;Configuration loaded from the motor controller.&lt;/p&gt;&lt;/body&gt;&lt;/html&gt;</meta_description>
</MCConfiguration>

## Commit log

2022-08-07 updated f3z design to pre-final
    [airspeed.step]
2022-10-14 restructured, updated 3d files and params
    [Front_base.stl, Front_base_test.stl, Front_cover.stl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]
2023-07-31 latest from january
    [HOUND.param]
2023-11-08 latest from hound
    [Front_base.stl, Front_cover d435.stl, Front_cover d455.stl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]
2024-02-06 refactored hardware files
    [D455_holder.stl, Front_base.stl, Front_cover d435.stl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]
2024-03-20 added DAWG param file for mro
    [DAWG_mro.param, HOUND_mro_defaults.param]
2024-06-16 added VESC files
    [hound_vesc.xml]
2024-06-16 Update README.md
    Added VESC instructions. Thanks to Jack for pointing this out!
2024-06-23 updated 3D print files
    [D455_holder.stl, Front_base.stl, Front_cover V4.stl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]
2024-07-10 updated hardware files
    [D455_holder.stl, Front_cover d435.stl, Front_cover d455.stl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]
2024-08-05 added lidar mount for new lidar, added traxass slash adapter dxf
    [LIDAR mount new.stl, traxass_adapter.dxf]
2024-08-05 added traxass slash step file
    [traxass_adapter v2.step]
2024-09-20 updated VESC orientation ambiguity.
